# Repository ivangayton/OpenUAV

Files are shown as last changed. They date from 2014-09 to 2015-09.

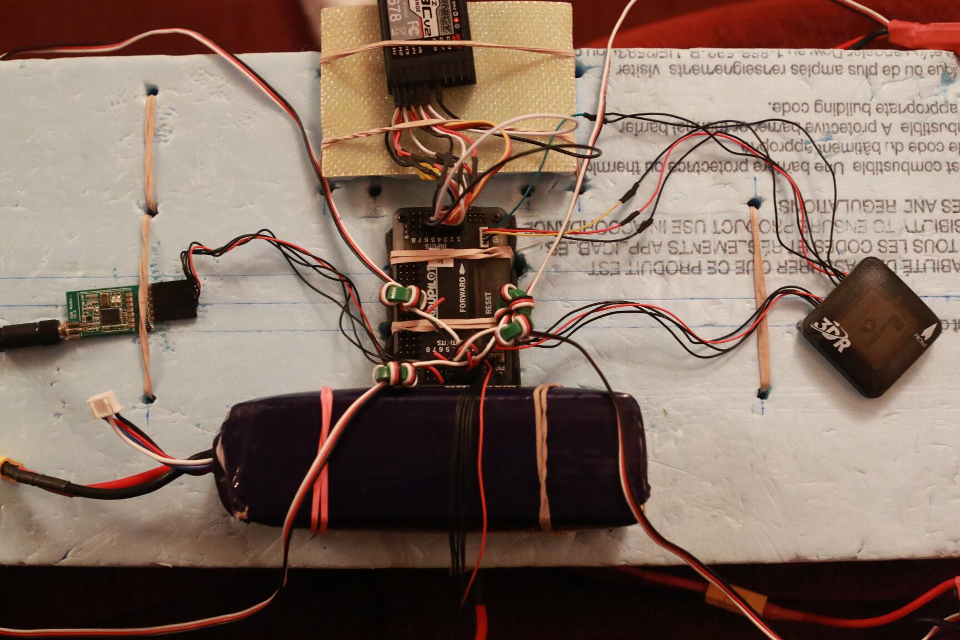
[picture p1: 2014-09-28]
Photos/IBGL0124 Electronics laid out.jpg

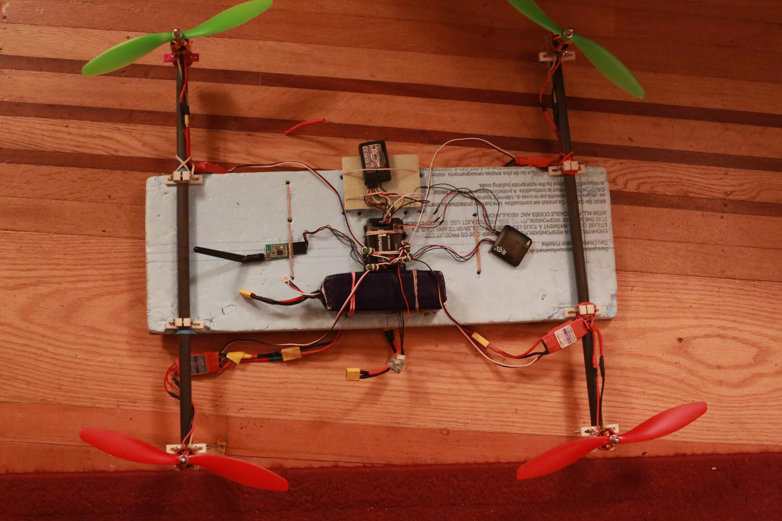
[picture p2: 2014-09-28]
Photos/IBGL0125 Whole quad with parts laid out.jpg

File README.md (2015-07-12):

OpenUAV
=======

This is intended to be a repository for design files, instructions, photos, documentation, and everything else needed for people wishing to build a and operate UAV (drone) in a low-income, resource-poor environment.  This is not about cutting-edge UAVs, it's about democratizing the technology and getting it into the hands of more people, particularly in poorer countries and humanitarian settings.

This repository focuses on hardware and builds, not software (we recommend using one of the excellent open-source software suites found at dronecode.org).  We will publish, where appropriate, recipes for setting up open-source software to specifically work with the hadware recipes here, but will not be developing software.  

The intended utilization is (at least initially) humanitarian activities, particularly mapping.  The dream: civil society, universities, and Non-Governmental Organizations (particularly small, local ones) are able to own and operate eyes in the sky, gathering their own aerial imagery rather than being dependent on governments, large companies, and international organizations.  This is intended to support such initiatives as missingmaps.org, openaerialmap.org, and http://opendronemap.github.io/odm/.  

We recommend adhering to the principles and code of conduct at uaviators.org, where additionally a great many resources, and a lively humanitarian UAV/drone user community can be found.

This repo is a work in progress.  For now it's focused on quad-copters, basically providing a drop-in, low-cost replacement for platforms like the 3DR IRIS+ or DJI Phantom, specifically adapted for resource-poor settings.  As time goes on, we'll be publishing files and recipes for fixed-wing UAVs, VTOL devices, and larger multicopters.  

Please feel free to comment, make requests, or pitch in.  If there's another, similar initiative that we should be backing instead of continuing with this repo, let us know; we don't want to duplicate efforts and if you're well ahead of us we would be happy to support your repo instead.

Let's get up in the air!

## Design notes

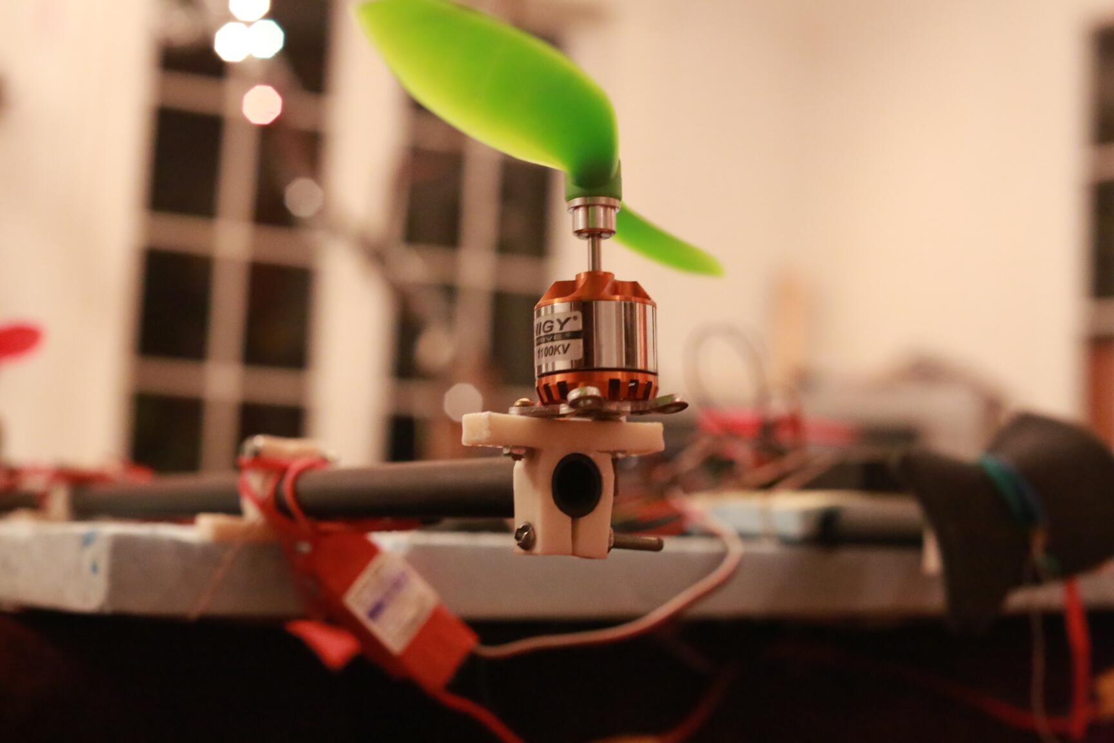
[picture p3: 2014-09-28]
Photos/IBGL0118 Motor and mount.jpg

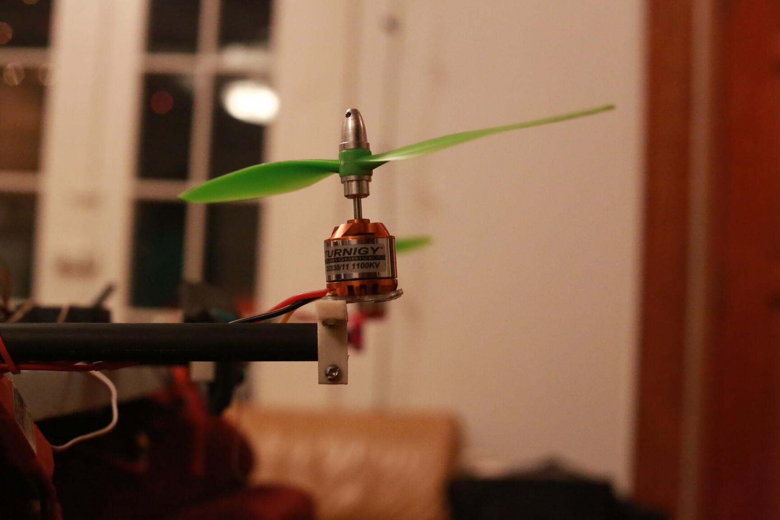
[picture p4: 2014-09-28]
Photos/IBGL0117 Motor and mount.jpg

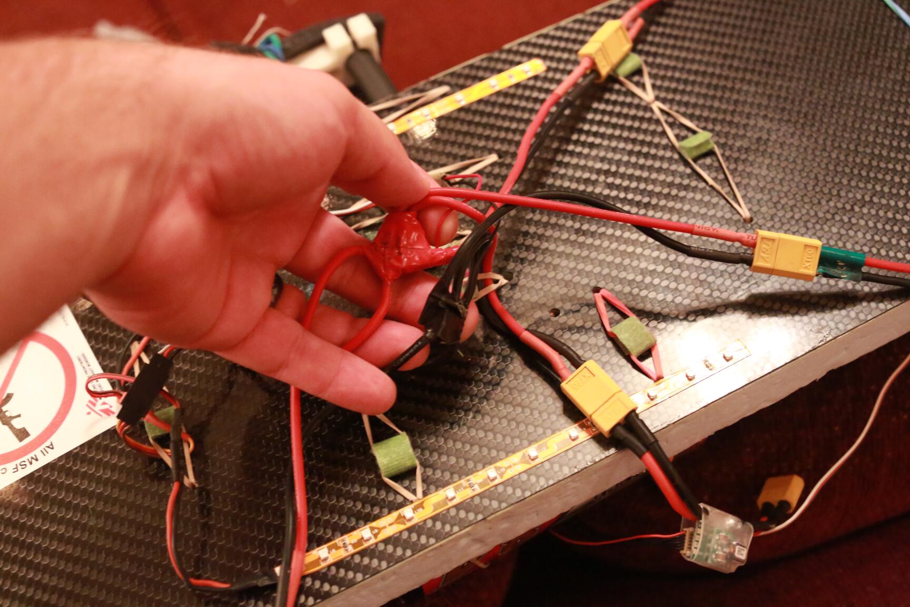
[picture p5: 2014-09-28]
Photos/IBGL0119 power distribution lump.jpg

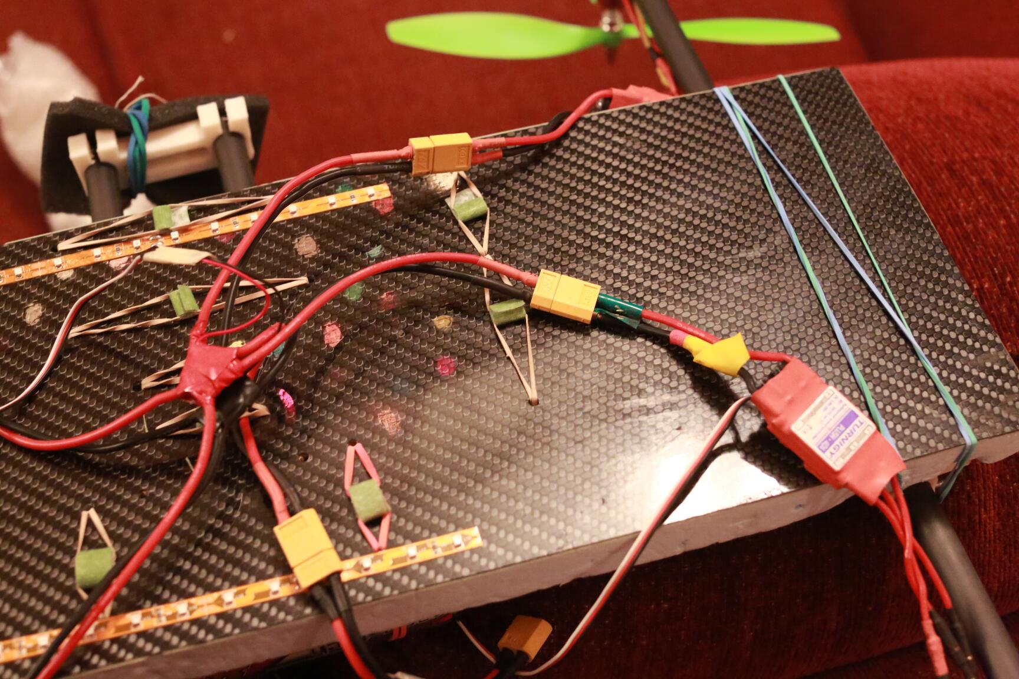
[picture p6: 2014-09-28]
Photos/IBGL0122 Power distribution lump.jpg

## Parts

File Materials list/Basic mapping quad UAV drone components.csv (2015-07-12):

Item | Price (USD) | Units | Subtotal | Link | £255.70
Ardupilot kit | $179.99 | 1 | $179.99 | http://hobbyking.com/hobbyking/store/__58283__HKPilot_Mega_2_7_Master_Set_With_OSD_LEA_6H_GPS_Power_module_Telemetry_Radio_915Mhz_XT_60_.html
Motors | $13.20 | 4 | $52.80 | http://hobbyking.com/hobbyking/store/__18969__Turnigy_D2836_8_1100KV_Brushless_Outrunner_Motor.html
Speed controllers | $13.15 | 4 | $52.60 | http://hobbyking.com/hobbyking/store/__2164__TURNIGY_Plush_30amp_Speed_Controller.html
Battery | $37.07 | 1 | $37.07 | http://hobbyking.com/hobbyking/store/__26795__Turnigy_5800mAh_3S_25C_Lipo_Pack_UK_Warehouse_.html
Radio | $59.99 | 1 | $59.99 | http://hobbyking.com/hobbyking/store/__8992__Turnigy_9X_9Ch_Transmitter_w_Module_8ch_Receiver_Mode_2_v2_Firmware_.html
Servo wires | $1.80 | 1 | $1.80 | http://hobbyking.com/hobbyking/store/__61681__10CM_Male_to_Male_Servo_Lead_JR_26AWG_10pcs_set_.html
Power wire red | $2.20 | 2 | $4.40 | http://hobbyking.com/hobbyking/store/__9673__Turnigy_Pure_Silicone_Wire_12AWG_1mtr_RED.html
Power wire black | $2.20 | 2 | $4.40 | http://hobbyking.com/hobbyking/store/__9674__Turnigy_Pure_Silicone_Wire_12AWG_1mtr_BLACK.html
Propellers green | $2.88 | 2 | $5.76 | http://www.hobbyking.com/hobbyking/store/__25820__10x4_5_SF_Props_2pc_CW_2pc_CCW_Green_.html
Propellers red | $2.90 | 2 | $5.80 | http://www.hobbyking.com/hobbyking/store/__25821__10x4_5_SF_Props_2pc_Standard_Rotation_2_pc_RH_Rotation_Red_.html
XT-60 connectors | $3.99 | 2 | $7.98 | http://hobbyking.com/hobbyking/store/__9572__Nylon_XT60_Connectors_Male_Female_5_pairs_GENUINE.html
Bullet connectors | $4.24 | 2 | $8.48 | http://hobbyking.com/hobbyking/store/__4136__Gold_Plated_Spring_Connector_3_5mm_10pair_20pc_.html
Charger | $28.99 | 1 | $28.99 | http://hobbyking.com/hobbyking/store/__11341__Turnigy_MAX80W_7A_Lithium_Polymer_Battery_Charger.html
Insulation foam | $37.79 | 0.2 | $7.56 | http://www.homedepot.ca/product/foamular-c-300-extruded-polystyrene-rigid-insulation-24-inch-x-96-inch-x-2-/905952

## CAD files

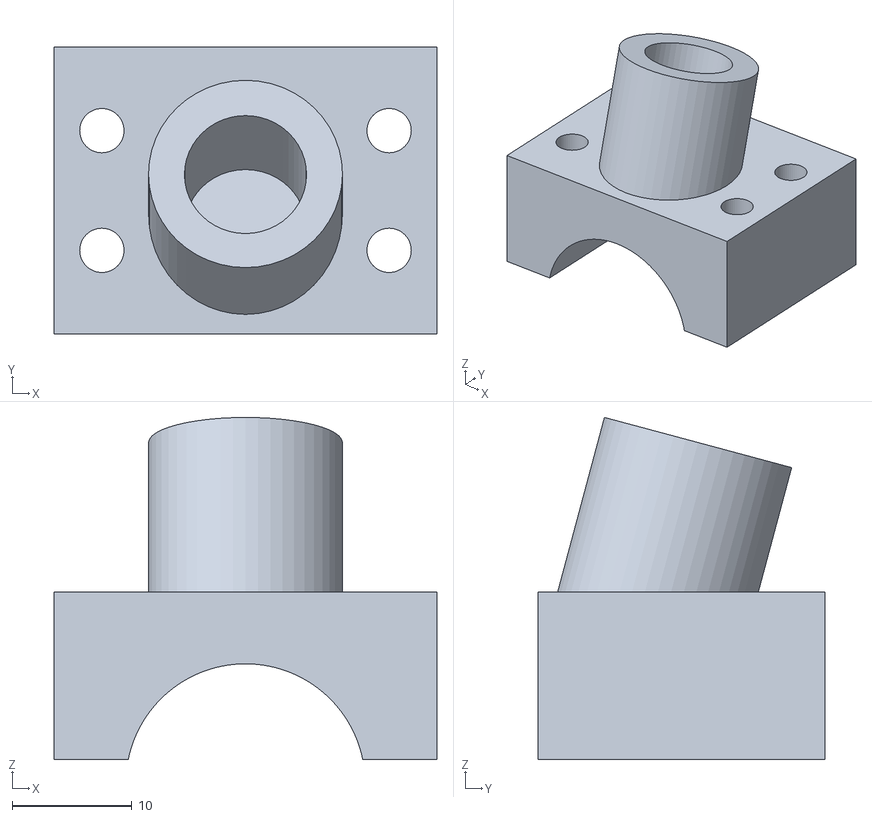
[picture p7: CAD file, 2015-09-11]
CAD files/STL files for printing/Motor mount bottom clamp for 20mm bamboo spar with leg holder.stl
32.0 x 24.0 x 28.6

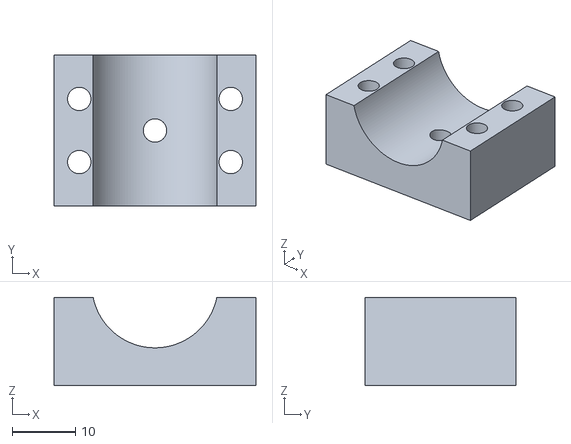
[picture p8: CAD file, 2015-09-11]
CAD files/STL files for printing/Motor mount bottom clamp for 20mm bamboo spar.stl
32.0 x 24.0 x 14.0

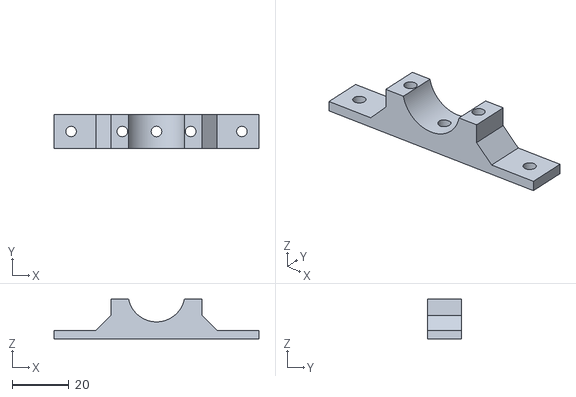
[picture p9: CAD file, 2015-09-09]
CAD files/STL files for printing/Spar T-mount half-width for 20mm bamboo.stl
72.0 x 12.0 x 14.0

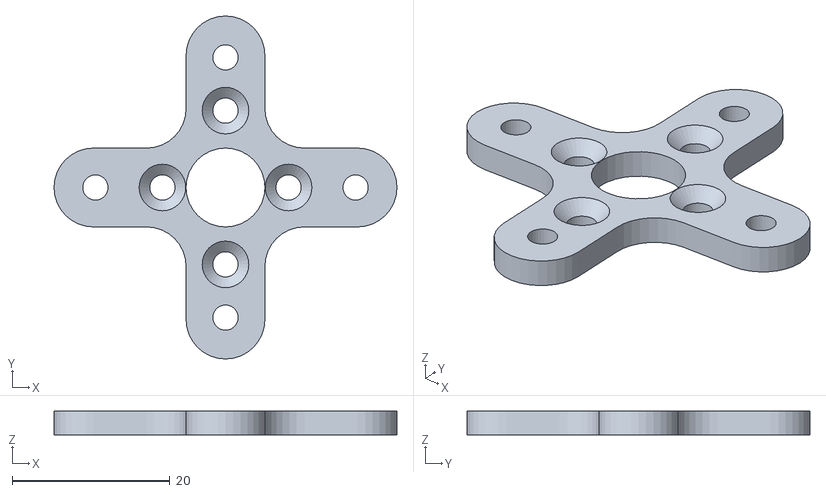
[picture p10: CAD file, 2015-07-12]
CAD files/STL files for printing/Motor_mount_X.stl
43.5 x 43.5 x 3.00

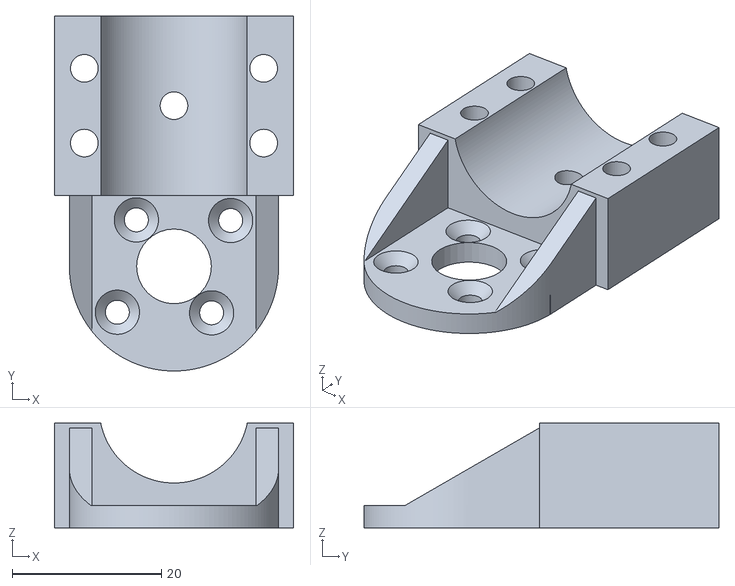
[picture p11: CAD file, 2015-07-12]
CAD files/STL files for printing/Motor mount for 20mm bamboo spar and D2830 motor.stl
32.0 x 47.5 x 14.0

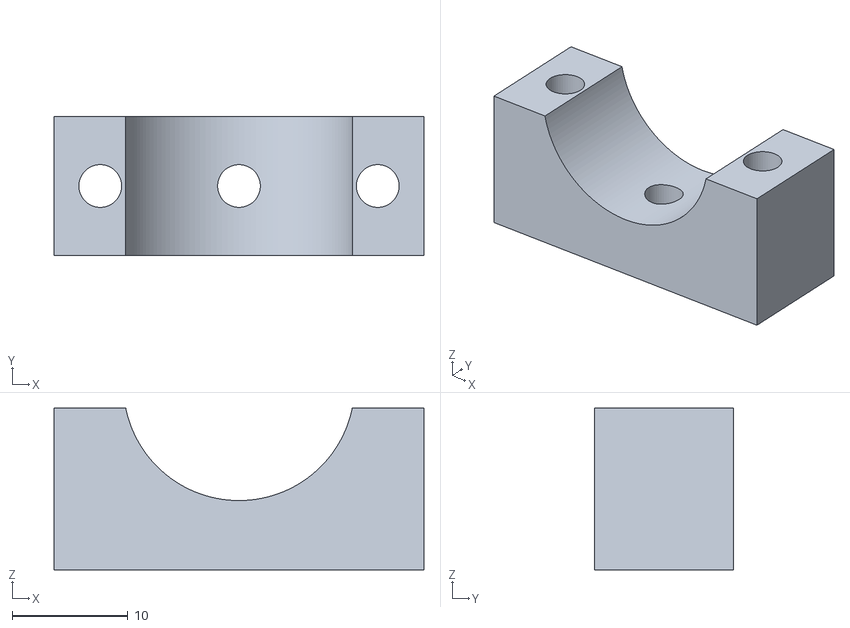
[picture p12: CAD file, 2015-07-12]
CAD files/STL files for printing/Motor mount bottom clamp half-width for 20mm bamboo spar.stl
32.0 x 12.0 x 14.0

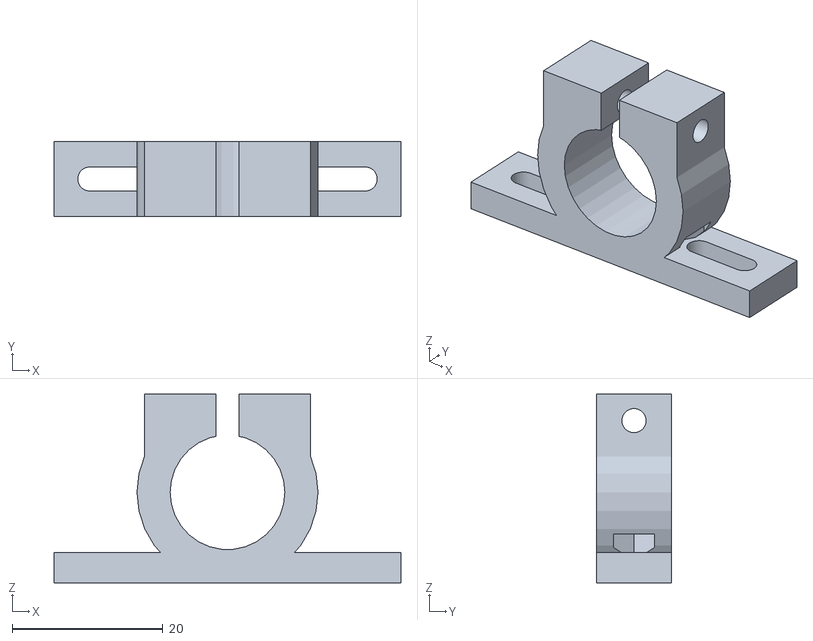
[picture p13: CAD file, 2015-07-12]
CAD files/STL files for printing/Tmount 15mm rod 10mm thickness.stl
46.0 x 10.0 x 25.0

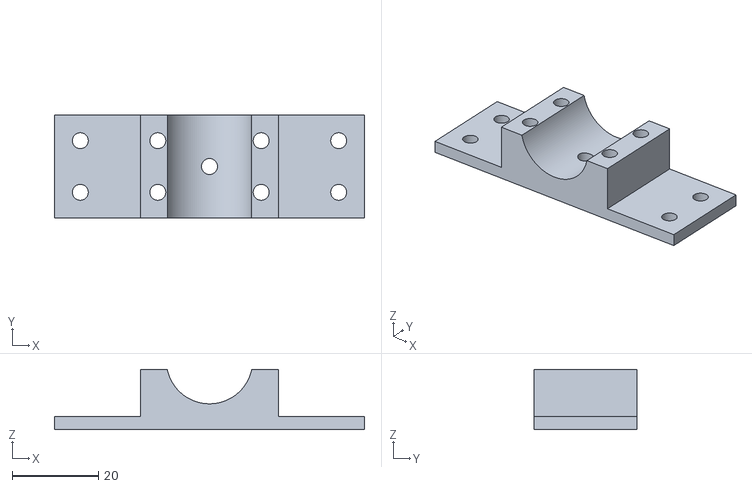
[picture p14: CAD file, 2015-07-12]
CAD files/STL files for printing/Spar T-mount for 20mm bamboo.stl
72.0 x 24.0 x 14.0

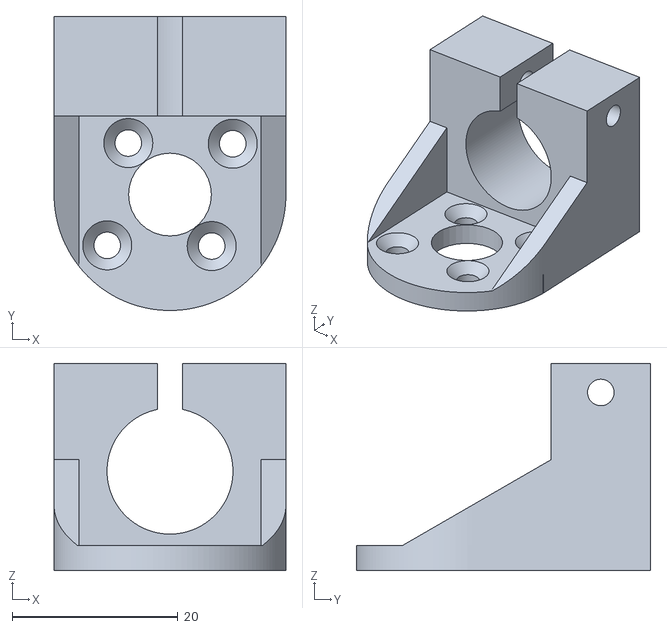
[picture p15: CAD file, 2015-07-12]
CAD files/STL files for printing/Combo_motor_mount_for_15mm_spar_D2830_motor.stl
28.0 x 35.5 x 25.0

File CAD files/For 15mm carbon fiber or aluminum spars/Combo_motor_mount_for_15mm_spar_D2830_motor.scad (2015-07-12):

module clamp_body()
{
  difference()
  {
    union()
    {  
      // main body around spar hole
      cube([28,22,12], center=true);
      //translate([0,2,0])
      // ring to thicken material around spar hole
      //cylinder(h=12, r=12, center=true,$fn=128);
    }
      union()
      {
      translate([0,-5,0])
      // notch below spar hole for tightening
        cube([3,15,14], center=true);
      translate([0,2,0])
      // main hole for spar
        cylinder(h=14, r=7.6, center=true,$fn=128);
      translate([0,-7.5,0])
        rotate(90,[0,1,0])
          // hole for tightening screw
          cylinder(h=100, r=1.6, center=true,$fn=128);
        }
  }
 
}

module plate()
{
union()
  {
  cylinder(r=14,h=3,$fn=48,center=true,$fn=128);
  translate([0,10.5,0])
  cube([28,22,3],center=true);
  }
}

module centralHole(diam)
{
cylinder(r=diam/2,h=3.2,$fn=32,center=true);
}

module screwholes()
{
translate([8,0,0])
  {
  cylinder(r=1.6,h=10,$fn=32,center=true,$fn=128);
  }
translate([-8,0,0])
  {
  cylinder(r=1.6,h=10,$fn=32,center=true,$fn=128);
  }
translate([0,9.75,0])
  {
  cylinder(r=1.6,h=10,$fn=32,center=true,$fn=128);
  }
translate([0,-9.75,0])
  {
  cylinder(r=1.6,h=10,$fn=32,center=true,$fn=128);
  }

}

module countersinks()
{
translate([8,0,0])
  {
  cylinder(r1=1.6,r2=3,h=1.55,$fn=32,$fn=128);
  }
translate([-8,0,0])
  {
  cylinder(r1=1.6,r2=3,h=1.55,$fn=32,$fn=128);
  }
translate([0,9.75,0])
  {
  cylinder(r1=1.6,r2=3,h=1.55,$fn=32,$fn=128);
  }
translate([0,-9.75,0])
  {
  cylinder(r1=1.6,r2=3,h=1.55,$fn=32,$fn=128);
  }
}

module buttresses()
{
difference()
  {
  union()
    {
    translate([12.5,0,6.4])
      difference()
        {
        cube([3,20,12],center=true);
        rotate(30,[1,0,0])
          translate([0,0,6])
            cube([4,28,12],center=true);
        }
    translate([-12.5,0,6.4])
      difference()
        {
        cube([3,20,12],center=true);
        rotate(30,[1,0,0])
          translate([0,0,6])
            cube([4,28,12],center=true);
        }
    }
    difference()
    {   
    cylinder(h=40,r=20,center=true);
    cylinder(h=50,r=14,center=true,$fn=128);
    translate([-50,0,-25])
      cube([100,100,100]);
    }
  }
}

module motorMount()
{
union()
  {
  difference()
    {
    plate();
    centralHole(10);
    rotate(129,[0,0,1])
      {
      screwholes();
      countersinks();
      }
    }
  buttresses();
  translate([0,15.5,12.5])
  rotate(270,[1,0,0])
  clamp_body();
  }
}

motorMount();

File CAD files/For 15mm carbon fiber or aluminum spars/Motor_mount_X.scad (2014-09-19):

module braceArm(width)
{
hull()
  {
  translate([33.5/2,0,0])
  cylinder(r=width/2,h=3,$fn=32,center=true);
  translate([-33.5/2,0,0])
  cylinder(r=width/2,h=3,$fn=32,center=true);
  }
}

module hub(brace_width){
hub=brace_width*2;
divot_rad=brace_width/2;
difference()
  {
  cube([hub,hub,3],center=true);
  translate([brace_width,brace_width,0])
  cylinder(r=divot_rad,h=5,$fn=32,center=true);
  translate([-brace_width,brace_width,0])
  cylinder(r=divot_rad,h=5,$fn=32,center=true);
  translate([brace_width,-brace_width,0])
  cylinder(r=divot_rad,h=5,$fn=32,center=true);
  translate([-brace_width,-brace_width,0])
  cylinder(r=divot_rad,h=5,$fn=32,center=true);
  }
}

module centralHole(diam)
{
cylinder(r=diam/2,h=10,$fn=32,center=true);
}

module screwholes()
{
translate([8,0,0])
  {
  cylinder(r=1.6,h=10,$fn=32,center=true);
  }
translate([-8,0,0])
  {
  cylinder(r=1.6,h=10,$fn=32,center=true);
  }
translate([0,9.75,0])
  {
  cylinder(r=1.6,h=10,$fn=32,center=true);
  }
translate([0,-9.75,0])
  {
  cylinder(r=1.6,h=10,$fn=32,center=true);
  }
translate([16.5,0,0])
  {
  cylinder(r=1.6,h=10,$fn=32,center=true);
  }
translate([-16.5,0,0])
  {
  cylinder(r=1.6,h=10,$fn=32,center=true);
  }
translate([0,16.5,0])
  {
  cylinder(r=1.6,h=10,$fn=32,center=true);
  }
translate([0,-16.5,0])
  {
  cylinder(r=1.6,h=10,$fn=32,center=true);
  }
}

module countersinks()
{
translate([8,0,0])
  {
  cylinder(r1=1.6,r2=3,h=1.55,$fn=32);
  }
translate([-8,0,0])
  {
  cylinder(r1=1.6,r2=3,h=1.55,$fn=32);
  }
translate([0,9.75,0])
  {
  cylinder(r1=1.6,r2=3,h=1.55,$fn=32);
  }
translate([0,-9.75,0])
  {
  cylinder(r1=1.6,r2=3,h=1.55,$fn=32);
  }
}

module motorMount()
{
brace_width=10;
difference()
  {
  union()
    {
    braceArm(brace_width);
    rotate(90,[0,0,1])
    braceArm(brace_width);
    hub(brace_width);
    }
  centralHole(10);
  screwholes();
  countersinks();
  }
}

motorMount();

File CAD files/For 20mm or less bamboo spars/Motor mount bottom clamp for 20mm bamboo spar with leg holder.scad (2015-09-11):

module clamp_body()
{
screw_hole_r=1.85; // for 3.5mm screws
leg_rad=5.1; // for a 10mm leg 
  difference()
    {
    // main body around spar hole
    union(){
      cube([32,24,14], center=true);
      translate([0,-2.5,-5])
      rotate(15,[1,0,0])
      cylinder(h=30,r=leg_rad+3,center=true,$fn=48);
    }
    union()
      {
      translate([0,0,9])
        // main notch for spar
        rotate(90,[1,0,0])
        cylinder(h=50, r=10, center=true,$fn=128);

      // hole for leg
      translate([0,2,-22])
      rotate(15,[1,0,0])
      #cylinder(h=40,r=leg_rad,center=true,$fn=48);

      // Holes along side rails for bolting alongside spar
      translate([12,-5,-20])
      cylinder(h=40,r=screw_hole_r,centre=true,$fn=48);
      translate([-12,-5,-20])
      cylinder(h=40,r=screw_hole_r,centre=true,$fn=48);
      translate([12,5,-20])
      cylinder(h=40,r=screw_hole_r,centre=true,$fn=48);
      translate([-12,5,-20])
      cylinder(h=40,r=screw_hole_r,centre=true,$fn=48);
      
    }
  }
 
}

rotate(180,[0,1,0])
clamp_body();

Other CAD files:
CAD files/For 20mm or less bamboo spars/Motor mount bottom clamp for 20mm bamboo spar.scad
CAD files/For 15mm carbon fiber or aluminum spars/Tmount 15mm rod 10mm thickness.scad
CAD files/For 20mm or less bamboo spars/Motor mount bottom clamp half-width for 20mm bamboo spar.scad
CAD files/For 20mm or less bamboo spars/Motor mount for 20mm bamboo spar and D2830 motor.scad
CAD files/For 20mm or less bamboo spars/Motor_mount_20mm_bamboo_spar_MultiStar_2212-920_motor.scad
CAD files/For 20mm or less bamboo spars/Spar T-mount bottom half-width for 20mm bamboo.scad
CAD files/For 20mm or less bamboo spars/Spar T-mount for 20mm bamboo.scad
CAD files/For 20mm or less bamboo spars/Spar T-mount half-width for 20mm bamboo.scad

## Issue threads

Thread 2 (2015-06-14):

Foam and carbon fiber body

smathermather, 2015-06-14:
Awesome project, @ivangayton. What are your specs for foam and carbon fiber sheet + rods?

ivangayton, 2015-06-30:
Foam: current best practice is 2-inch rigid polystyrene insulation foam:
http://www.homedepot.ca/product/foamular-c-300-extruded-polystyrene-rigid-insulation-24-inch-x-96-inch-x-2-/905952

Using this rigid foam with a good thickness removes the necessity for carbon fiber sheet.

The rods I used in the previous build were 15mm carbon fiber  from Rockwest Composites (pretty much any 15mm rods will work, and that's a common size because it's the standard for camera rails):
http://www.rockwestcomposites.com/search?term=45409&x=0&y=0

However, I no longer use this!  I've moved to 20mm bamboo stakes!  I'll put up a link shortly

smathermather, 2015-07-02:
Does the [CAD file](https://github.com/ivangayton/OpenUAV/blob/master/CAD%20files/Tmount%2015mm%20rod%2010mm%20thickness.scad) work OK with 20mm bamboo stakes, or does it need modified?

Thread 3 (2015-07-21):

Power Distribution Lump

dakotabenjamin, 2015-07-21:
Is it just 5 12AWG wires soldered together and wrapped up in tape? Is the thinner wire for LEDs? I can't tell from the pictures.

ivangayton, 2015-07-22:
Hi,

It's a soldered "star" of 12guage wires.  Have a look at the instructions I've just put on the wiki:

https://github.com/ivangayton/OpenUAV/wiki/04-Construction-instructions

I'll put some better photos up as soon as I can!  Right now travelling a lot so hard to get the pics in a nice workshop environment.

Ivan

Date: Tue, 21 Jul 2015 06:23:42 -0700
From: notifications@github.com
To: OpenUAV@noreply.github.com
Subject: [OpenUAV] Power Distribution Lump (#3)

Is it just 5 12AWG wires soldered together and wrapped up in tape? Is the thinner wire for LEDs? I can't tell from the pictures.

—
Reply to this email directly or view it on GitHub.

dakotabenjamin, 2015-07-22:
Great! Thanks.

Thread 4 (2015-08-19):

We built it, now we need help powering up

dakotabenjamin, 2015-08-19:
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

As far as I can tell, everything here is correctly built. I can't find which output ports each ESC goes into the output of the controller, but I figured I'd put them anywhere until I get the whole thing to stop beeping.

I also got the transmitter matched with the receiver. Where do I go from here?

dakotabenjamin, 2015-08-19:
Other Questions:
 * What kind of configuration settings are needed in Mission Planner?
 * How do we fit all the components on the board while maintaining a reasonable center of gravity?

ivangayton, 2015-08-19:
Wow, this looks great!  Yes, this looks well-built.  You may need to trim your foam a bit more; I suspect that your props will be over the foam on the inside part of their travel, causing you to lose lift.  You may want to move the spars further out as well; in general the further apart the motors are the more stable the quad will be.

Ok, a few answers:
First, here's the most important set of instructions for the software:

http://copter.ardupilot.com/wiki/initial-setup/

So you first need to install either Mission Planner (Windows) or APM Planner 2 (I use this as I'm on Linux).  Either one will allow you to flash the firmware onto your autopilot using a USB cable.  Instructions on the wiki.

Then you need to wire everything up (again, everything on the wiki, specifically here: http://copter.ardupilot.com/wiki/initial-setup/assembly-instructions/connecting-the-apm2/)

Keep following the ArduCopter wiki, step by step.  It's pretty generic, not specific to any particular hardware, though of course you are using the APM rather than the PixHawk (the wiki is increasingly built around the PixHawk, but the APM is perfectly capable and much cheaper so for now I'm still using it).

As for Center of Gravity, I tend to put my flight controller dead centre, and the battery just behind it (see the photo here https://github.com/ivangayton/OpenUAV/blob/master/Photos/IBGL0125%20Whole%20quad%20with%20parts%20laid%20out.jpg).  Of course, this puts the centre of gravity toward the rear of the quad.  The quad can handle a bit of that, but of course it means your rear motors are working harder.  I usually mount my camera way up front, which counterbalances the battery, and has the added bonus of, if I want to film facing forward, getting the camera well out in front and taking less pictures of propellers and more of the scenery.  So, provided you want to mount a camera (which in my case often amounts to a cellphone hanging over the front edge facing down), the rear-mounted battery is actually an advantage.

I strongly recommend putting some dampening foam under your spar mounts and flight controller.  Vibration is bad!  Cheapo packing foam is fine.  or upholstery foam (I got all the dampening foam I could ever use for free from an upholstery shop, which had an unlimited supply of odd-sized off-cuts.

We should talk: I'm happy to help with setup and it'll be easier if we can chat on the phone or Skype.  Stephen has my email/number!
Ivan

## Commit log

2014-09-19 Added t-mount design file in OpenSCAD format
    [Tmount 15mm rod 10mm thickness.scad]
2014-09-19 Added motor X-mount design file in OpenSCAD format
    [Motor_mount_X.scad]
2014-09-19 Added spreadsheet with materials list
    [Basic mapping quad UAV drone components.csv]
2015-06-14 fix broken Ardupilot kit link
    [Basic mapping quad UAV drone components.csv]
2015-06-30 Added a link for procurement of insulation foam
    [Basic mapping quad UAV drone components.csv]
2015-07-12 Changed prices to USD, slight changes to URLs to reflect available products on Hobbyking website.
    [Basic mapping quad UAV drone components.csv]
2015-07-12 Deleted an old STL file
    [Motor mount bottom clamp for 20mm bamboo spar.scad, Motor mount with 20mm radius notch and tightening screws for bamboo spars.stl, Spar T-mount for 20mm bamboo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]
2015-07-12 cleaning old files
    [Motor mount with 20mm radius notch and tightening screws for bamboo spars.stl]
2015-07-12 Added main bamboo motor mount CAD file
    [Motor mount for 20mm bamboo spar and D2830 motor.scad]
2015-07-12 Added a bunch of CAD files for mounting motors on bamboo spars, added STL files for printing of same.
    [Combo_motor_mount_for_15mm_spar_D2830_motor.scad, Combo_motor_mount_for_15mm_spar_D2830_motor.stl, Motor mount bottom clamp for 20mm bamboo spar.stl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]
2015-07-12 Updated materials list with wires
    [Basic mapping quad UAV drone components.csv]
2015-09-07 Added a gcode file for the bamboo motor mount
2015-09-09 A few improvements to t-mount and other slight changes
    [Spar T-mount half-width for 20mm bamboo.scad, Spar T-mount half-width for 20mm bamboo.stl]
2015-09-09 Added some gcode files for Reprap Mendel - not applicable to other printers
    [Motor mount bottom clamp for 20mm bamboo spar with leg holder.scad, Motor mount bottom clamp for 20mm bamboo spar with leg holder.stl]
2015-09-09 Organized folders for different spar sizes and types.
    [Combo_motor_mount_for_15mm_spar_D2830_motor.scad, Motor mount bottom clamp for 20mm bamboo spar with leg holder.scad, Motor mount bottom clamp for 20mm bamboo 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]
2015-09-11 Fixed a measurement error in the bottom bracket with leg holder
    [Motor mount bottom clamp for 20mm bamboo spar with leg holder.scad, Motor mount bottom clamp for 20mm bamboo spar with leg holder.stl, Motor mount bottom clamp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]
2020-02-01 added missing bottom half of spar mount clamp
    [Motor_mount_20mm_bamboo_spar_MultiStar_2212-920_motor.scad, Spar T-mount bottom half-width for 20mm bamboo.scad]
2020-02-01 uncomment spar holes
    [Spar T-mount bottom half-width for 20mm bamboo.scad]
